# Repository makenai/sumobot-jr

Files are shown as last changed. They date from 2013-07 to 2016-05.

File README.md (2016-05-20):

# Sumobot Jr.

Sumobot Jr. is an open source sumobot design made for [Nodebots Day](http://nodebotsday.com). Most existing sumo kits cost between $99 and $160. Since we're trying to keep our event costs down, I decided to try to design a bot that could be put together for around $50 including the cost of the Arduino. The name and design are inspired by the simplicity and zip-tied wooden beauty of the [Printrbot Jr](http://printrbot.com/).

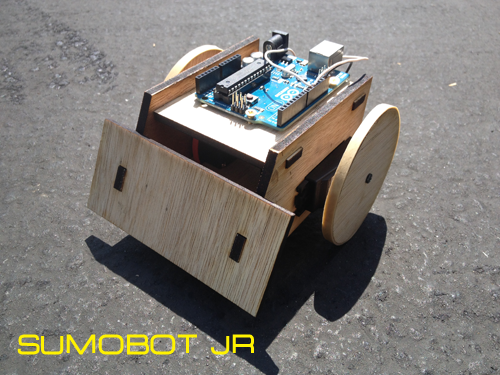
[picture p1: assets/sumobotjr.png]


## How ?

If you're planning on laser cutting the bots, you should use the OpenSCAD source file to generate a cutting plan for your specific type of laser cutter and material thickness. There's a wiki article for that!

[Laser Cutting with the OpenSCAD file](https://github.com/makenai/sumobot-jr/wiki/Working-with-the-OpenSCAD-file)

If you want to jump right into it, you can watch this instructional video, but note that you may not want to clip the wires if you plan to reuse the servos for something else:

[Sumobot Jr Assembly video for Nodebots Day 7/27](http://www.youtube.com/watch?v=0Q3hrKUwxDM)

[Customizing Sumobot Jr with Suziam and cats](http://www.youtube.com/watch?v=BB0vihv9ylM)

[IKEA-style Assembly Instruction Card](http://makenai.github.io/sumobot-jr/sumobot-instructions.pdf)

[Microsoft's version for Build 2015 on Raspberry Pi + Windows 10](https://www.youtube.com/watch?v=aKCieb-Gf2g)

[Katie K's No Solder Guide](http://katiek2.github.io/sumobot-nosolder/)

[Frank Hunleth's Arduino Mini Shield](https://oshpark.com/shared_projects/TEsKZkdg)

[Norfolk.js's Shopping List](https://github.com/norfolkjs/general-info/wiki/Norfolk.js-SumoBot-Kits)

[Sidepart adaptors for MG-6-48 DC-Motors from ghtomcat](https://github.com/ghtomcat/sumobot)

The main part of the design is a cutting sheet in EPS file format that is designed to be used with a laser cutter. You can find it in the cutting_plans directory. If you don't have a laser cutter, you can use a CNC, tape your printout to balsa wood and go at it with an x-acto knife, or send it to a laser cutting service like [Ponoko](https://www.ponoko.com/) and get the sheet done for about $10.

There is also a directory called 3d_print that contains an STL file for a ball caster designed by [sliptonic](http://www.thingiverse.com/thing:13782) - the STL is set up for a 16mm ball bearing, but you can make one for other sizes with the included OpenSCAD file.

**NEW** Microsoft has created a tutorial and version of the bot kit for [Build 2015](http://www.buildwindows.com/). You can find their version of the cutting plan for Ponoko in this repository, and also check out their [tutorial using Raspberry Pi and Windows 10](http://microsoft.hackster.io/windowsiot/robot-kit).

There is a completely 3D printable version available at [Thingiverse](http://www.thingiverse.com/thing:357369) now.

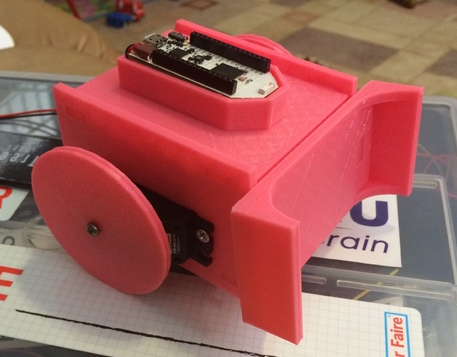
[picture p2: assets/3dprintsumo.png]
[](http://www.thingiverse.com/thing:357369)

## What if I don't have a Laser Cutter / 3D Printer?!

Neither do I! The best way to get some help creating the parts is to look up your local [Hackerspace or Makerspace ](http://hackerspaces.org) and connect with them. I belong to a fantastic hackerspace in Las Vegas called [SYN Shop](http://synshop.org)!

[](http://synshop.org)

If you don't have a hackerspace nearby, you can also use a mail order service like [Ponoko](http://ponoko.com) that does both 3D printing and laser cutting.

## Other Parts Needed

+ [Arduino](https://www.pololu.com/product/2191) - ~$25
+ [4xAA battery holder](http://www.amazon.com/gp/product/B007Q2NR1O/ref=oh_aui_search_detailpage?ie=UTF8&amp;psc=1) - $2
+ 2 Zip ties - ?
+ 5 \#4 3/8" wood screws - ?
+ Thick rubber bands - ?
+ 2 continuous servo motors like [Futaba S148](http://www.pololu.com/catalog/product/536) or the ones from [SpringRC](http://www.pololu.com/product/1248) - $24-$28
+ Some wire or leads
+ 16mm ball bearing - ?

## No-solder Wiring Diagram (thanks @katiek2)



That's about it! Connect the red and black leads on the servos together, then connect them to the + and - terminals on the battery holder respectively. Then connect the black leads and - terminal to the ground of the Arduino. Finally, the white leads of each motor go to pins 9 and 10 (or whatever you like) on the Arduino - you're done!

## Sample Code

To run the sample code for the Sumobot Jr., you will first need to install [Node.js](http://nodejs.org/) and [git](https://git-scm.com).

Open a terminal application and clone this repository:
```
git clone https://github.com/makenai/sumobot-jr
```

Navigate to the code folder:
```
cd code_example
```

Install code dependencies:

```
npm i
```

Run the code:

```
node sumobot.js
```

## License

[Creative Commons - Attribution - ShareAlike 3.0](http://creativecommons.org/licenses/by-sa/3.0/)

You are free to:

+ to Share — to copy, distribute and transmit the work, and
+ to Remix — to adapt the work
+ Under the following conditions:
    + Attribution — You must attribute the work in the manner specified by the author or licensor (but not in any way that suggests that they endorse you or your use of the work)
    + Share Alike — If you alter, transform, or build upon this work, you may distribute the resulting work only under the same, similar or a compatible license.

With the understanding that:

+ Waiver — Any of the above conditions can be waived if you get permission from the copyright holder.
+ Other Rights — In no way are any of the following rights affected by the license:
    + your fair dealing or fair use rights;
    + the author's moral rights; and
    + rights other persons may have either in the work itself or in how the work is used, such as publicity or privacy rights.

## Credits

Made by

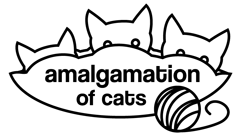
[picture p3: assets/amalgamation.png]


Design by [@makenai](http://twitter.com/makenai) with feedback and ideas from [@noopkat](http://twitter.com/noopkat) aka (by their powers combined) Amalgamation of Cats.

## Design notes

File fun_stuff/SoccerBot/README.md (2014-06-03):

##SoccerBot Mod

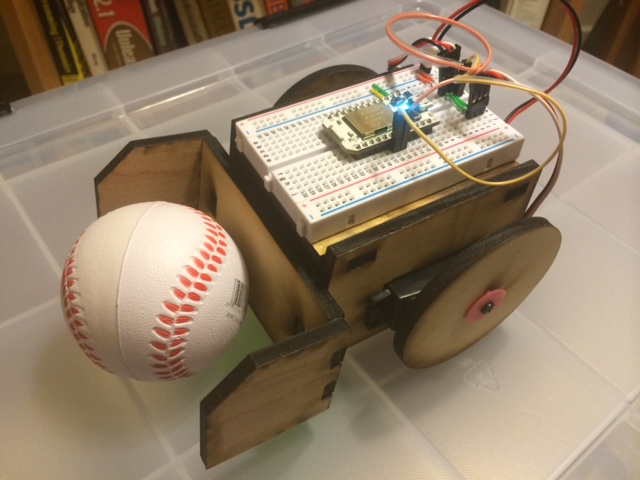
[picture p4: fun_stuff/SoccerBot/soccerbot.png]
SoccerBot


These modifications were created quickly and dirtily for the [JSConf 2014](http://2014.jsconf.us/) SoccerBot tournament. Just replacement wheels, shovel and a 3D printable wheel hub that is an improvement over the old wooden method!

Video (https://www.youtube.com/watch?v=CcCwjnWBoJ8)

Want to see the matches?

Video (https://www.youtube.com/watch?v=kE-g8LFVeYw)

Video (https://www.youtube.com/watch?v=HgWbxDNJleQ)

Video (https://www.youtube.com/watch?v=ViGQqndk6Og)

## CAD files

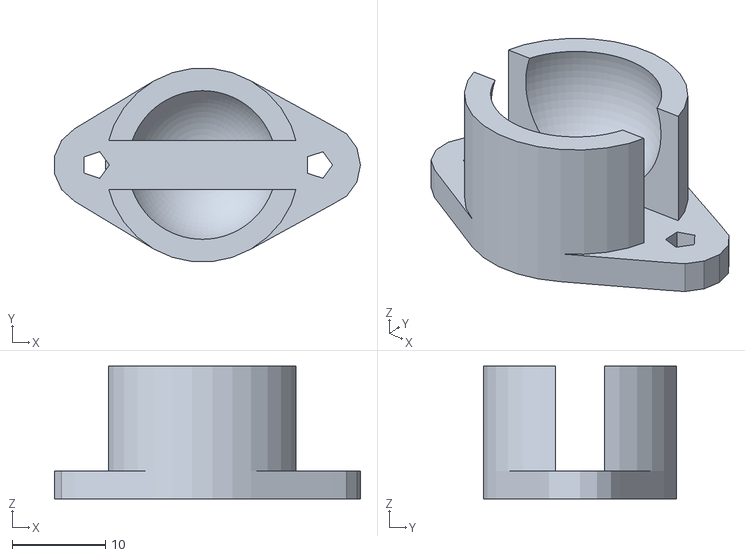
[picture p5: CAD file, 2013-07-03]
3d_print/BallCaster.stl
32.9 x 20.8 x 14.3

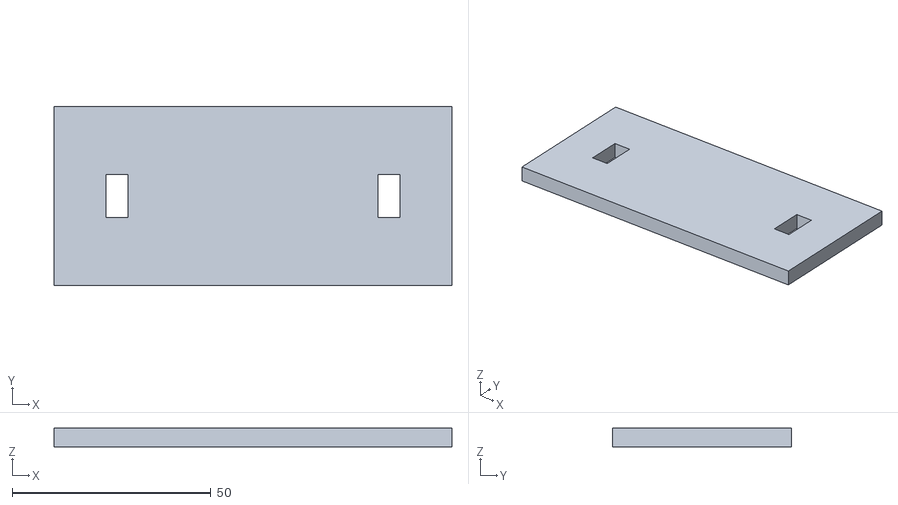
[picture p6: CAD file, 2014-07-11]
3d_print/sumobot/front-flat.stl
100.0 x 45.0 x 4.75

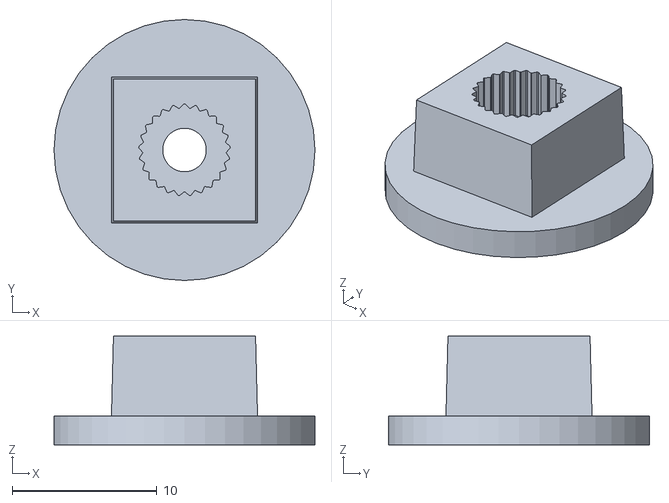
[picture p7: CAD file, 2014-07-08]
fun_stuff/SoccerBot/WheelHub.stl
18.0 x 18.0 x 7.50

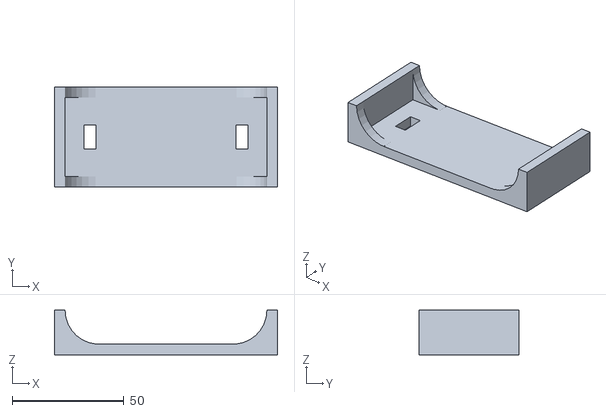
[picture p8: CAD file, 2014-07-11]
3d_print/sumobot/front-curved.stl
100.0 x 45.0 x 20.0

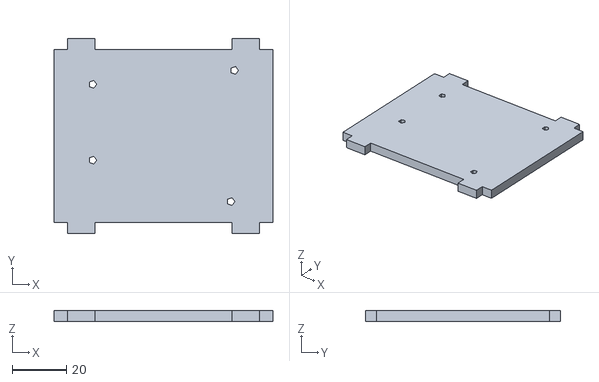
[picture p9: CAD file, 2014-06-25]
3d_print/sumobot/top-arduino.stl
80.5 x 71.5 x 4.00

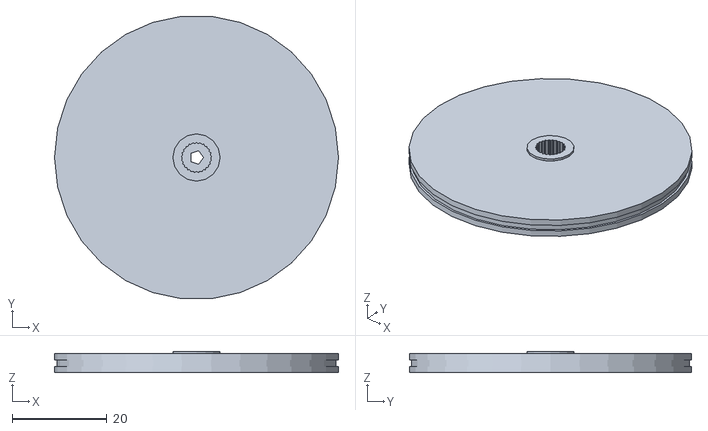
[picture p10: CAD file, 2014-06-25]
3d_print/sumobot/wheel.stl
60.0 x 59.7 x 4.50

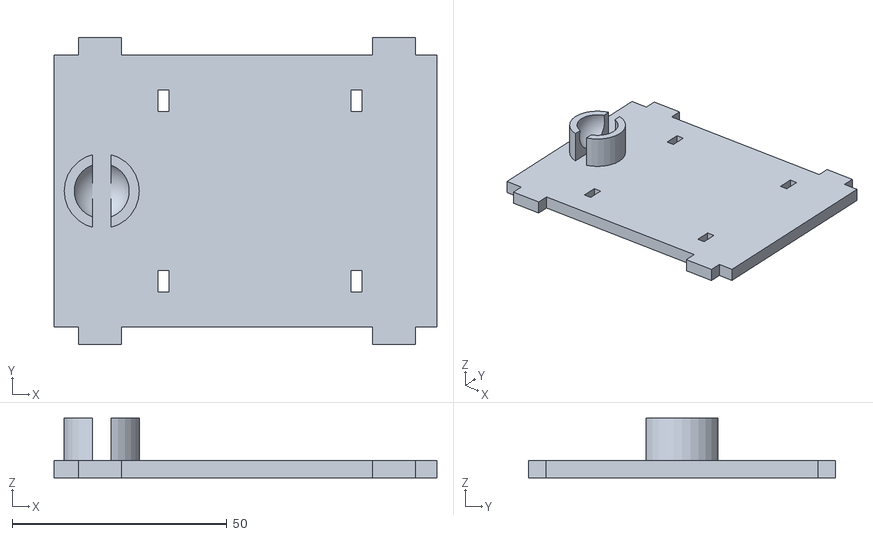
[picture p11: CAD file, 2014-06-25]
3d_print/sumobot/bottom.stl
89.3 x 71.5 x 13.9

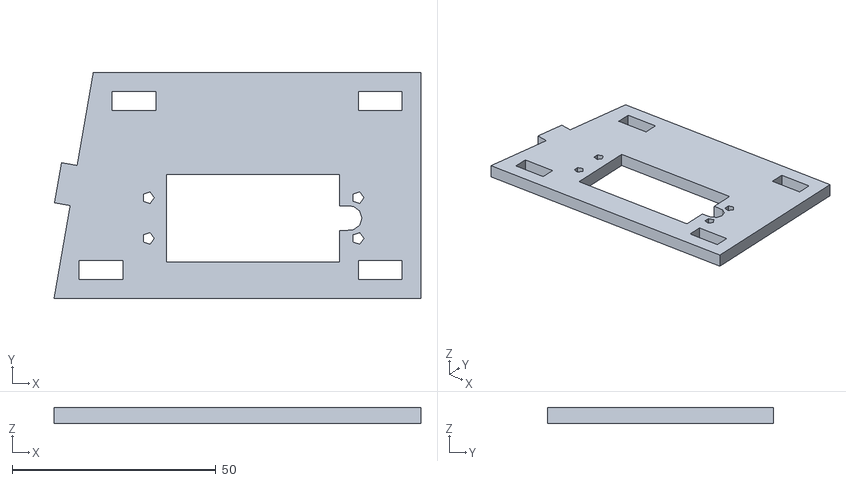
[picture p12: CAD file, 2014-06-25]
3d_print/sumobot/side.stl
90.1 x 55.5 x 4.00

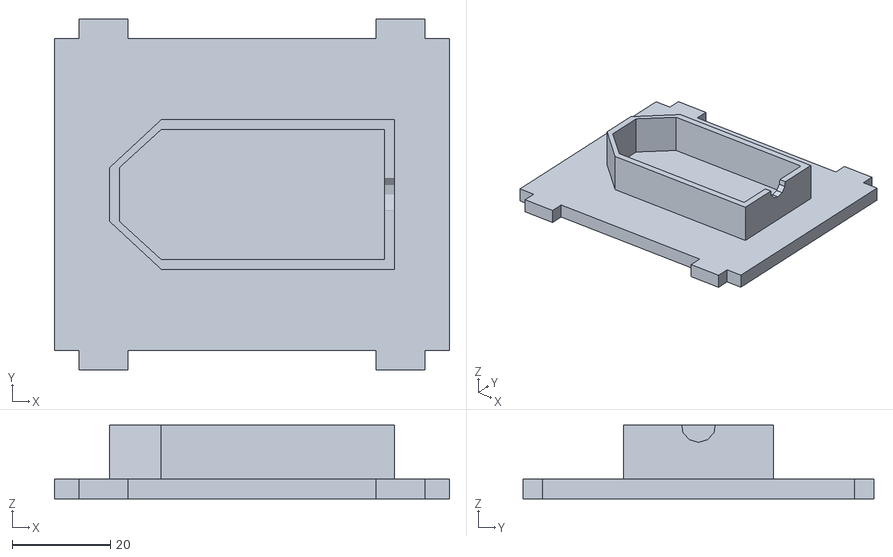
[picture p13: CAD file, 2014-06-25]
3d_print/sumobot/top-pinoccio.stl
80.5 x 71.5 x 15.0

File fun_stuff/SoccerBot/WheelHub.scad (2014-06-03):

/**
 *  Parametric servo arm generator for OpenScad
 *  Générateur de palonnier de servo pour OpenScad
 *
 *  Copyright (c) 2012 Charles Rincheval.  All rights reserved.
 *
 *  This library is free software; you can redistribute it and/or
 *  modify it under the terms of the GNU Lesser General Public
 *  License as published by the Free Software Foundation; either
 *  version 2.1 of the License, or (at your option) any later version.
 *
 *  This library is distributed in the hope that it will be useful,
 *  but WITHOUT ANY WARRANTY; without even the implied warranty of
 *  MERCHANTABILITY or FITNESS FOR A PARTICULAR PURPOSE.  See the GNU
 *  Lesser General Public License for more details.
 *
 *  You should have received a copy of the GNU Lesser General Public
 *  License along with this library; if not, write to the Free Software
 *  Foundation, Inc., 51 Franklin St, Fifth Floor, Boston, MA  02110-1301  USA
 *
 *  Last update :
 *  https://github.com/hugokernel/OpenSCAD_ServoArms
 *
 *  http://www.digitalspirit.org/
 */

$fn = 40;

/**
 *  Clear between arm head and servo head
 *  With PLA material, use clear : 0.3, for ABS, use 0.2
 */
SERVO_HEAD_CLEAR = 0.2;

/**
 *  Head / Tooth parameters
 *  Futaba 3F Standard Spline
 *  http://www.servocity.com/html/futaba_servo_splines.html
 *
 *  First array (head related) :
 *  0. Head external diameter
 *  1. Head heigth
 *  2. Head thickness
 *  3. Head screw diameter
 *
 *  Second array (tooth related) :
 *  0. Tooth count
 *  1. Tooth height
 *  2. Tooth length
 *  3. Tooth width
 */
FUTABA_3F_SPLINE = [
    [6, 4, 1.1, 2.5],
    [25, 0.3, 0.7, 0.1]
];

module servo_futaba_3f(length, count) {
    servo_arm(FUTABA_3F_SPLINE, [length, count]);
}

/**
 *  If you want to support a new servo, juste add a new spline definition array
 *  and a module named like servo_XXX_YYY where XXX is servo brand and YYY is the
 *  connection type (3f) or the servo type (s3003)
 */

module servo_standard(length, count) {
    servo_futaba_3f(length, count);
}

/**
 *  Tooth
 *
 *    |<-w->|
 *    |_____|___
 *    /     \  ^h
 *  _/       \_v
 *   |<--l-->|
 *
 *  - tooth length (l)
 *  - tooth width (w)
 *  - tooth height (h)
 *  - height
 *
 */
module servo_head_tooth(length, width, height, head_height) {
    linear_extrude(height = head_height) {
        polygon([[-length / 2, 0], [-width / 2, height], [width / 2, height], [length / 2,0]]);
    }
}

/**
 *  Servo head
 */
module servo_head(params, clear = SERVO_HEAD_CLEAR) {

    head = params[0];
    tooth = params[1];

    head_diameter = head[0];
    head_heigth = head[1];

    tooth_count = tooth[0];
    tooth_height = tooth[1];
    tooth_length = tooth[2];
    tooth_width = tooth[3];

    % cylinder(r = head_diameter / 2, h = head_heigth + 1);

    cylinder(r = head_diameter / 2 - tooth_height + 0.03 + clear, h = head_heigth);

    for (i = [0 : tooth_count]) {
        rotate([0, 0, i * (360 / tooth_count)]) {
            translate([0, head_diameter / 2 - tooth_height + clear, 0]) {
                servo_head_tooth(tooth_length, tooth_width, tooth_height, head_heigth);
            }
        }
    }
}

/**
 *  Servo hold
 *  - Head / Tooth parameters
 *  - Arms params (length and count)
 */
module servo_arm(params, arms) {

    head = params[0];
    tooth = params[1];

    head_diameter = head[0];
    head_heigth = head[1];
    head_thickness = head[2];
    head_screw_diameter = head[3];

    tooth_length = tooth[2];
    tooth_width = tooth[3];

    arm_length = arms[0];
    arm_count = arms[1];

    /**
     *  Servo arm
     *  - length is from center to last hole
     */
    module arm(tooth_length, tooth_width, head_height, head_heigth, hole_count = 1) {

        arm_screw_diameter = 2;

        difference() {
            union() {
                cylinder(r = tooth_width / 2, h = head_heigth);

                linear_extrude(height = head_heigth) {
                    polygon([
                        [-tooth_width / 2, 0], [-tooth_width / 3, tooth_length],
                        [tooth_width / 3, tooth_length], [tooth_width / 2, 0]
                    ]);
                }

                translate([0, tooth_length, 0]) {
                    cylinder(r = tooth_width / 3, h = head_heigth);
                }

                if (tooth_length >= 12) {
                    translate([-head_heigth / 2 + 2, 3.8, -4]) {
                        rotate([90, 0, 0]) {
                            rotate([0, -90, 0]) {
                                linear_extrude(height = head_heigth) {
                                    polygon([
                                        [-tooth_length / 1.7, 4], [0, 4], [0, - head_height + 5],
                                        [-2, - head_height + 5]
                                    ]);
                                }
                            }
                        }
                    }
                }
            }

            // Hole
            for (i = [0 : hole_count - 1]) {
                //translate([0, length - (length / hole_count * i), -1]) {
                translate([0, tooth_length - (4 * i), -1]) {
                    cylinder(r = arm_screw_diameter / 2, h = 10);
                }
            }

            cylinder(r = head_screw_diameter / 2, h = 10);
        }
    }

    difference() {
        translate([0, 0, 0.1]) {
            cylinder(r = head_diameter / 2 + head_thickness, h = head_heigth + 1);
        }

        cylinder(r = head_screw_diameter / 2, h = 10);

        servo_head(params);
    }

    arm_thickness = head_thickness;

    // Arm
    translate([0, 0, head_heigth]) {
        for (i = [0 : arm_count - 1]) {
            rotate([0, 0, i * (360 / arm_count)]) {
                arm(arm_length, head_diameter + arm_thickness * 2, head_heigth, 2);
            }
        }
    }
}

module wheelhub() {
	translate([0,0,1])	
	difference() {
		union() {
			hull() {
				cube([10.1,10.1,1],center=true);
				translate([0,0,6]) {
					cube([9.8,9.8,1],center=true);
				}
			}
			cylinder(d=18,h=2,center=true);
		}
		translate([0,0,-10]) cylinder(d=3,h=20);
		translate([0,0,-1.1]) cylinder(d=4,h=1);
		translate([0,0,3]) servo_head(FUTABA_3F_SPLINE);
	}
}

wheelhub();

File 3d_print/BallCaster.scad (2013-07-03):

WallThickness = 2;
BallSize = 15.88;
Airgap = .5;
Mount = 3;
TotalHeight = 19.5;
MountScrewRad = 1.5;  //3mm screw
BallProtrude = .33; //percentage of ball radius sticking out 

MountType = 1;  //1=ears  2=center screw
ScrewSpacing = 25;


cylheight = TotalHeight;
cylrad = (BallSize/2) + WallThickness + Airgap;
echo (cylheight);
difference () {
	cylinder(r1 = cylrad , r2 = cylrad,  cylheight - (BallSize*BallProtrude));

	translate([0,0,TotalHeight - BallSize/2]) {
		cube(size = [cylrad*2+5, cylrad/2, BallSize*1.25], center = true );
		}

	translate([0,0,TotalHeight - (BallSize/2)]) {
		sphere (BallSize/2+Airgap, $fa=5, $fs=0.1);
		}
	}

difference (){
	linear_extrude(height=Mount)
	hull() {
		translate([ScrewSpacing/2,0,0]) {
			circle(  MountScrewRad*3);
			}
  		translate([1-ScrewSpacing/2,0,0]) {
			circle( MountScrewRad*3);
   			}
		circle( cylrad);
		}

	translate([ScrewSpacing/2,0,0]) {
		cylinder(r1 = MountScrewRad, r2 = MountScrewRad, h= Mount+2);
		}
  	translate([1-ScrewSpacing/2,0,0]) {
		cylinder(r1 = MountScrewRad, r2 = MountScrewRad, h= Mount+2);
   		}
}

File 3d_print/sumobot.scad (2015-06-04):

/*
 * =============================================================================
 * SumoBot Kit Master OpenSCAD File
 * =============================================================================
 * All measurements are in mm, because go metric or go home.
 */

 /* Build Flags - Variables to programatically select which part to output */

  build_laser_sheet = 1;
  build_wheel = 0;
  build_top = 0;
  build_shovel = 0;
  build_bottom = 0;
  build_side = 0;

/* Features Flags */

  // For 3D printing, we can have a curved or flat shovel
  curved_shovel = 0;

  // For 3D printing, we can include a ball caster on the bottom
  built_in_caster = 0;

  // For 3D printing, we can have a built in wheel hub
  built_in_hub = 1;

  // For 3D printing, we can select a pinoccio mount for the top
  pinoccio_top = 0;

/* Parameters */

  // Kerf is the amount of space removed by a cutting tool. I use it
  // here to describe how much space to leave between tabs and space.
  // For laser cutters, I use 0.05, for 3D printers I use 0.375
  kerf = 0.05;

  // How thick is the material? This also is the tab height.
  material_thickness = 4.75;

  // How high is the battery case?
  battery_case_height = 16;

  // How large is our servo hole?
  servo_height = 21.5;
  servo_length = 42.5;

  // How long is the sumo bot?
  sled_length = 80.5;

  // How wide is the sumo bot?
  sled_width = 63.5;

  // How close to the edge of the material do we place a tab?
  tab_edge_distance = 5;

  // How long are our tabs?
  tab_length = 10;

  // What is the angle that the sumobot shovel?
  ramp_angle = 80;

  // How wide is the shovel?
  shovel_width = 100;

  // How high is the shovel?
  shovel_height = 45;

  // Only for a 3D printed, curved shovel, how tall is the side?
  shovel_side_height = 20;

  // How big are our ziptie holes?
  ziptie_height = 5;
  ziptie_width = 2.5;

  // How big are the screw holes? 2.25mm is good for #4 wood screws
  screw_diameter = 2.25;

  // How far apart are our ball caster holes?
  caster_screw_spacing = 25;

  // How far back from the front do we place the caster?
  caster_position = 12;

  // How big are our wheels?
  wheel_radius = 30;

  // Caster Settings
  Caster_WallThickness = 2;
  Caster_BallSize = 12.5;
  Caster_Airgap = .5;
  Caster_TotalHeight = 14;
  Caster_BallProtrude = .33;

  // Servo Wheel
  SERVO_HEAD_CLEAR = 0.2;
  FUTABA_3F_SPLINE = [
      [6, 4, 1.1, 2.5],
      [25, 0.3, 0.7, 0.1]
  ];
  FUTABA_3F_SPLINE_KERF = [
      [6-(kerf/2), 4, 1.1, 2.5],
      [25, 0.3, 0.7, 0.1]
  ];

/* Calculated Values */

  // Tab spacing account for kerf
  tab_spacing = kerf * 2;

  // We figure out the side based on a snug fit for the battery case
  sled_height = ((material_thickness + tab_edge_distance) * 2 ) +
  	servo_height + battery_case_height;

  // Length of the ramp (bottom of the right triangle) depends on the angle
  ramp_length = cos( ramp_angle ) * sled_height;

  // We want to place the tab the correct tab distance on the bottom, so we need
  // to cut into the distance taken up by the ramp.
  ramp_tab_distance = cos(ramp_angle)*( tab_edge_distance + material_thickness);

  // The length of the sled plus the length of the ramp
  side_length = sled_length + ( cos( ramp_angle ) * (sled_height - tab_edge_distance) );

/* Utility Modules */

// A hole for a screw.
module screw_hole() {
	circle(d=screw_diameter);
}

// Male side of the tab
module tab() {
	square([tab_length, material_thickness]);
}

// Female side of the tab
module tab_hole() {
	translate([tab_spacing/-2,tab_spacing/-2])
		square([tab_length + tab_spacing, material_thickness +tab_spacing]);
}

// A ziptie hole
module ziptie_hole() {
	square([ziptie_width,ziptie_height]);
}

// Built-in ball caster
module caster() {
	cylheight = Caster_TotalHeight;
	cylrad = (Caster_BallSize/2) + Caster_WallThickness + Caster_Airgap;
	difference () {
		cylinder(r1 = cylrad , r2 = cylrad,  cylheight - (Caster_BallSize*Caster_BallProtrude));
		translate([0,0,Caster_TotalHeight - Caster_BallSize/2]) {
			cube(size = [cylrad*2+5, cylrad/2, Caster_BallSize*1.25], center = true );
		}
		translate([0,0,Caster_TotalHeight - (Caster_BallSize/2)]) {
			sphere (Caster_BallSize/2+Caster_Airgap, $fa=5, $fs=0.1);
		}
	}
}

// Servo mounting hole including a circular cutout for the wires
module servo_hole() {
	square([servo_length, servo_height]);
	// screw holes
	translate([-4.5,(servo_height/2)+5])
		screw_hole();
	translate([-4.5,(servo_height/2)-5])
		screw_hole();
	translate([servo_length+4.5,(servo_height/2)+5])
		screw_hole();
	translate([servo_length+4.5,(servo_height/2)-5])
		screw_hole();
	// wire hole
	hull() {
		translate([servo_length-1,servo_height/2])
			square(6,center=true);
		translate([servo_length+2.5,servo_height/2])
			circle(3,center=true);
	}

}

// Mounting holes for an arduino
module arduino_holes() {
	translate([-26.05,-24.1]) {
		translate([0, 15.2]) screw_hole();
		translate([0, 43.1]) screw_hole();
		translate([50.8, 0]) screw_hole();
		translate([52.1, 48.2]) screw_hole();
	}
}

// A special pinoccio shaped mount for the top of the bot
module pinoccio_mount() {
	height = 11;
	base_width = 26.5;
	base_length = 45.5;
	bevel_width = 11;
	bevel_length =8.5;
	wall_thickness = 2;
	plug_hole_size = 3.5;

	translate([base_length/-2-bevel_length/-2,-base_width/2])
	difference() {
		linear_extrude(height)
		hull() {
			translate([0,-wall_thickness])
				square([base_length + wall_thickness,base_width + wall_thickness*2]);
 			translate([-bevel_length - wall_thickness,base_width/2-bevel_width/2])
				square(bevel_width);
		}
		translate([0,0,-1])
		linear_extrude(height+2)
		hull() {
			square([base_length,base_width]);
			translate([-bevel_length,base_width/2-bevel_width/2])
				square(bevel_width);
		}
		translate([base_length-1, base_width/2,height])
			rotate([0,90])
			cylinder(r=plug_hole_size,h=wall_thickness+2);
	}
}

// The little curved part on the side of the curved shovel
module sloped_support(size) {
	difference() {
		cube([size,material_thickness,size]);
		translate([size,material_thickness+1,size])
			rotate([90])
			cylinder(r=size-material_thickness,h=material_thickness+2);
	}
}

// Side for a curved shovel (___)
module shovel_side() {
	cube([material_thickness,shovel_height,shovel_side_height]);
	sloped_support(shovel_side_height);
	translate([0,shovel_height-material_thickness])
		sloped_support(shovel_side_height);
}

module servo_head_tooth(length, width, height, head_height) {
    linear_extrude(height = head_height) {
        polygon([[-length / 2, 0], [-width / 2, height], [width / 2, height], [length / 2,0]]);
    }
}

// The little part that you can attach servo hubs to on a servo, used for the
// built in hub option of the wheel.
module servo_head(params, clear = SERVO_HEAD_CLEAR) {

    head = params[0];
    tooth = params[1];

    head_diameter = head[0];
    head_heigth = head[1];

    tooth_count = tooth[0];
    tooth_height = tooth[1];
    tooth_length = tooth[2];
    tooth_width = tooth[3];

	union() {
    cylinder(r = head_diameter / 2 + 0.1, h = head_heigth + 1);

    cylinder(r = head_diameter / 2 - tooth_height + 0.03 + clear, h = head_heigth);

    for (i = [0 : tooth_count]) {
        rotate([0, 0, i * (360 / tooth_count)]) {
            translate([0, head_diameter / 2 - tooth_height + clear, 0]) {
                servo_head_tooth(tooth_length, tooth_width, tooth_height, head_heigth);
            }
        }
    }
	}
}

// The little screw slot in the side of the sumo bot -
module wheel_screw_slot() {
	hull() {
		translate([0,0,-1])
			cylinder(d=screw_diameter,h=material_thickness+2);
		translate([0,8,-1])
			cylinder(d=screw_diameter,h=material_thickness+2);
	}
}

/* Parts */

// The side of the sumobot /___|
module side() {
	linear_extrude(height=material_thickness)
	difference() {

		union() {
			square([sled_length, sled_height]);
			polygon([[0,0], [0,sled_height], [-ramp_length,0]] );
			translate([-ramp_length/2,sled_height/2])
				rotate(ramp_angle)
				translate([-tab_length/2,-0.1])
				tab();
		}

		// Servo hole
		translate([sled_length - servo_length - tab_length - tab_edge_distance - tab_edge_distance,
				material_thickness + tab_edge_distance])
			servo_hole();

		// Bottom right
		translate([sled_length - tab_length - tab_edge_distance, tab_edge_distance])
			tab_hole();

		// Bottom Left
		translate([-ramp_length + ramp_tab_distance + tab_edge_distance,
				tab_edge_distance])
			tab_hole();

		// Top left
		translate([tab_edge_distance, sled_height - material_thickness - tab_edge_distance])
			tab_hole();

		// Top right
		translate([sled_length - tab_length - tab_edge_distance,
				sled_height - material_thickness - tab_edge_distance])
			tab_hole();
	}
}
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

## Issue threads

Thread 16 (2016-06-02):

Mounting hole options

dtex, 2016-06-02:
I'd like to add a parameter to the SCAD file for choosing different hole patterns for the top plate (Tessel 2 is my use case). Does that sound like a worthwhile PR?

makenai, 2016-06-02:
Yup - most certainly. Thanks for looking at the SCAD files instead of the vectors. :)

I think you should be able to add an parameter / method to it similar to the arduino and pinoccio ones here: https://github.com/makenai/sumobot-jr/blob/master/3d_print/sumobot.scad#L186

dtex, 2016-06-02:
Cool. I was thinking of adding a parameter like this:
````
// Mounting hole pattern
// valid values are "Arduino Uno", "Tessel 2"
hole_pattern = "Arduino Uno";
````
And then just add a conditional in ```top``` to call the right module.

dtex, 2016-06-05:
Hmmm, like most things it's never as easy as it seems. I had to make the sled wider to fit the mounting holes, but the GPIO ports are still kind of exposed (anything plugged in could be easily ripped out by another sumo).

Sigh...

I'll keep playing with it.

dtex, 2016-06-26:
I'm thinking it makes the most sense to have an option for Tessel mounting holes like we discussed, but then just have a note somewhere (the readme?) that gives the minimum sled width and a suggested sled length.

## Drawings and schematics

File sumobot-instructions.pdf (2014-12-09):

# SumoBot Kit

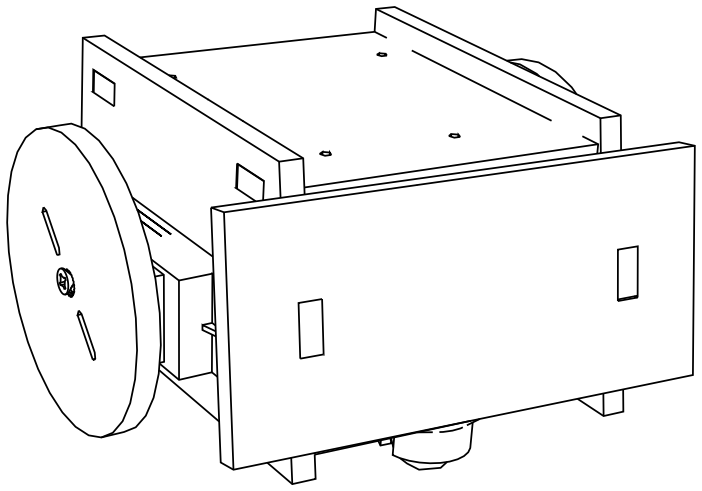
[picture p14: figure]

# http://sumobotkit.com

### (you can call it a PawelBot if you want to)

This simple yet versatile robot kit is ready to become your loyal companion! Unlike many robots you’ll see, this one is made of wood. That makes it very easy to glue, paint, drill, and customize to your heart’s content. There is a great personality in this wooden frame just waiting for you to release it!

See the assembly instructions on the flip side of this card. When it’s time to hook up a “brain” of your choosing, just remember:

- red (+) wires all go together
- black (-) wires go together and to a ground pin on your microcontroller
- white or yellow wires go to PWM capable pins on your microcontroller

If you find your motors move when you don’t want them to, you can center them with a screwdriver by turning the potentiometer on the back of each servo. Enjoy your new robot friend!

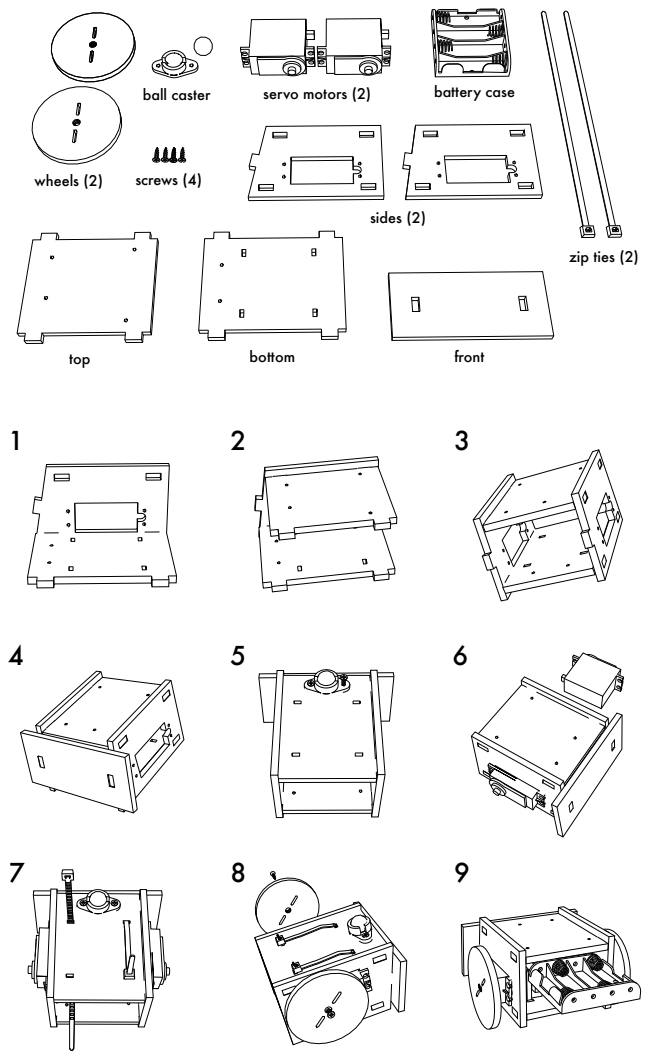
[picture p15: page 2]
wheels (2); screws (4); ball caster; servo motors (2); battery case; top; bottom; front; sides (2); zip ties (2)

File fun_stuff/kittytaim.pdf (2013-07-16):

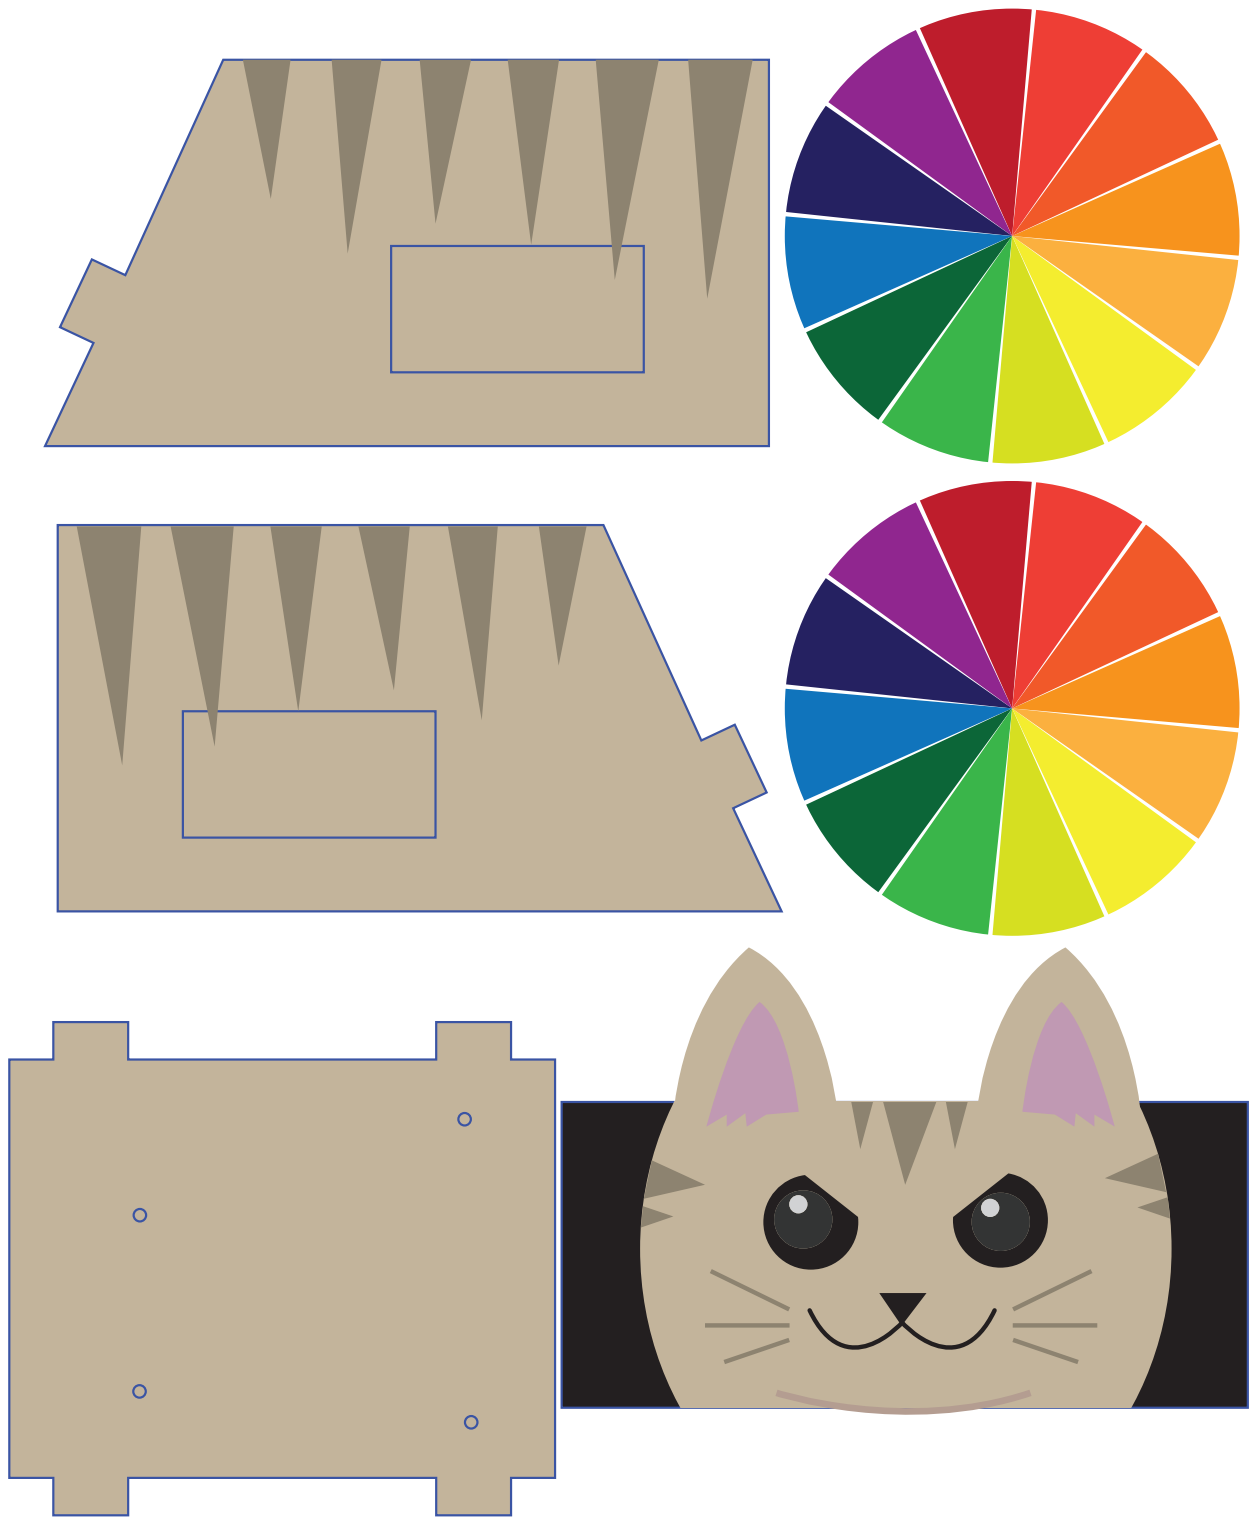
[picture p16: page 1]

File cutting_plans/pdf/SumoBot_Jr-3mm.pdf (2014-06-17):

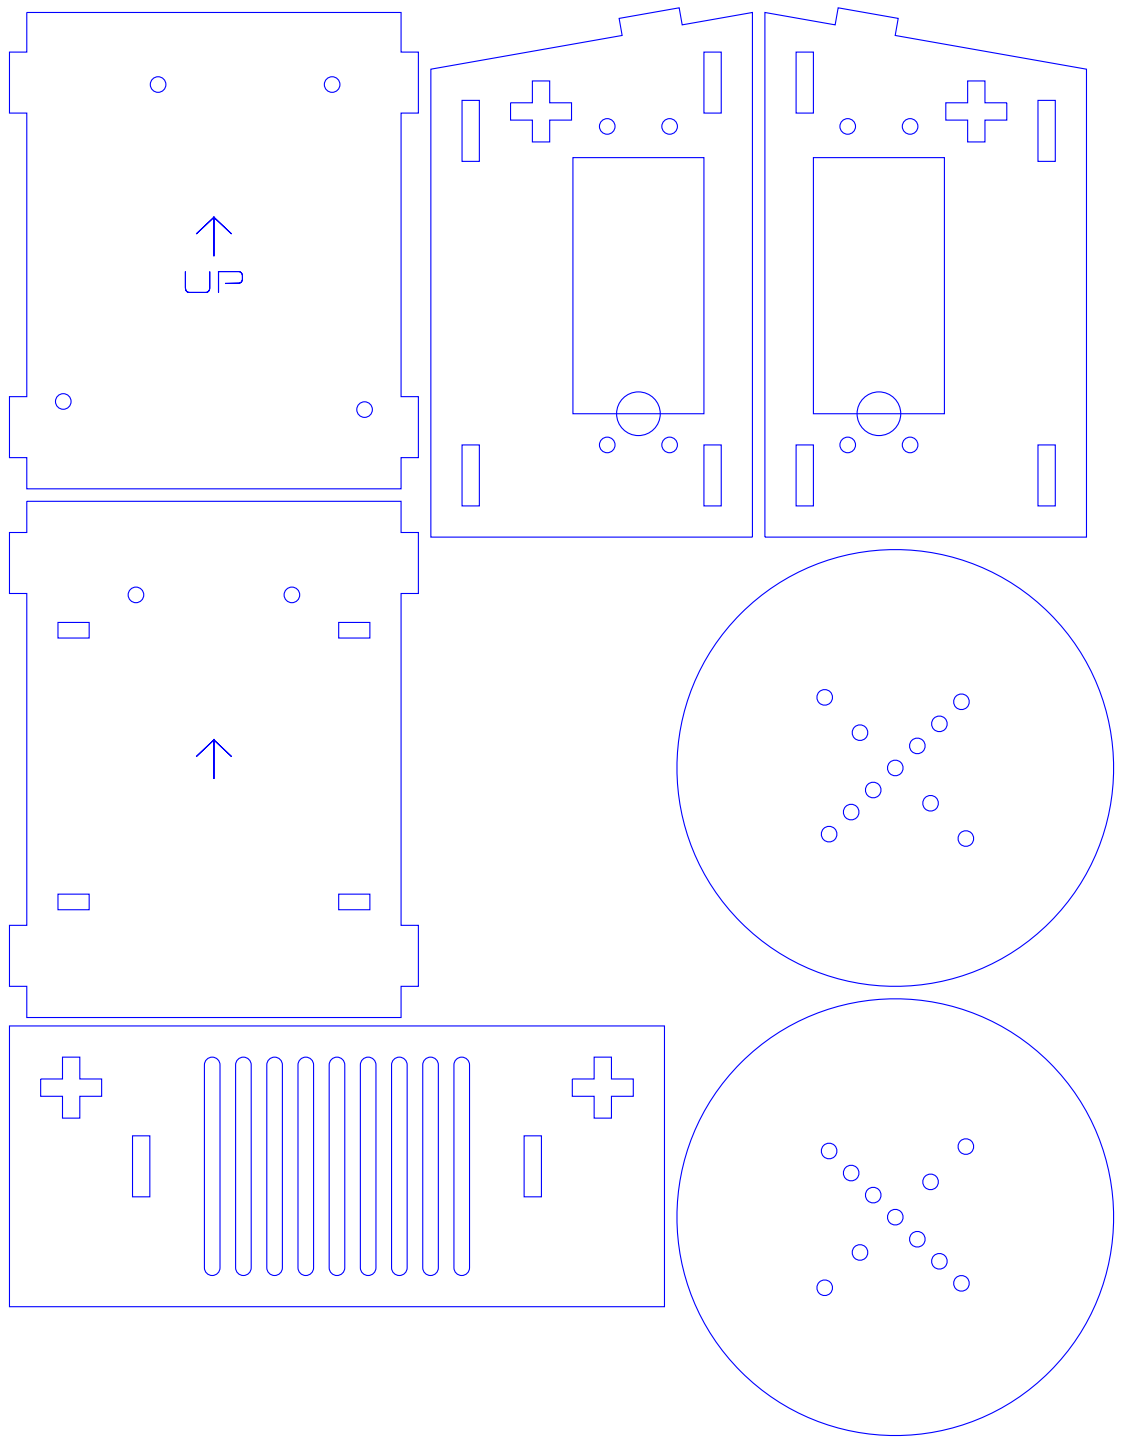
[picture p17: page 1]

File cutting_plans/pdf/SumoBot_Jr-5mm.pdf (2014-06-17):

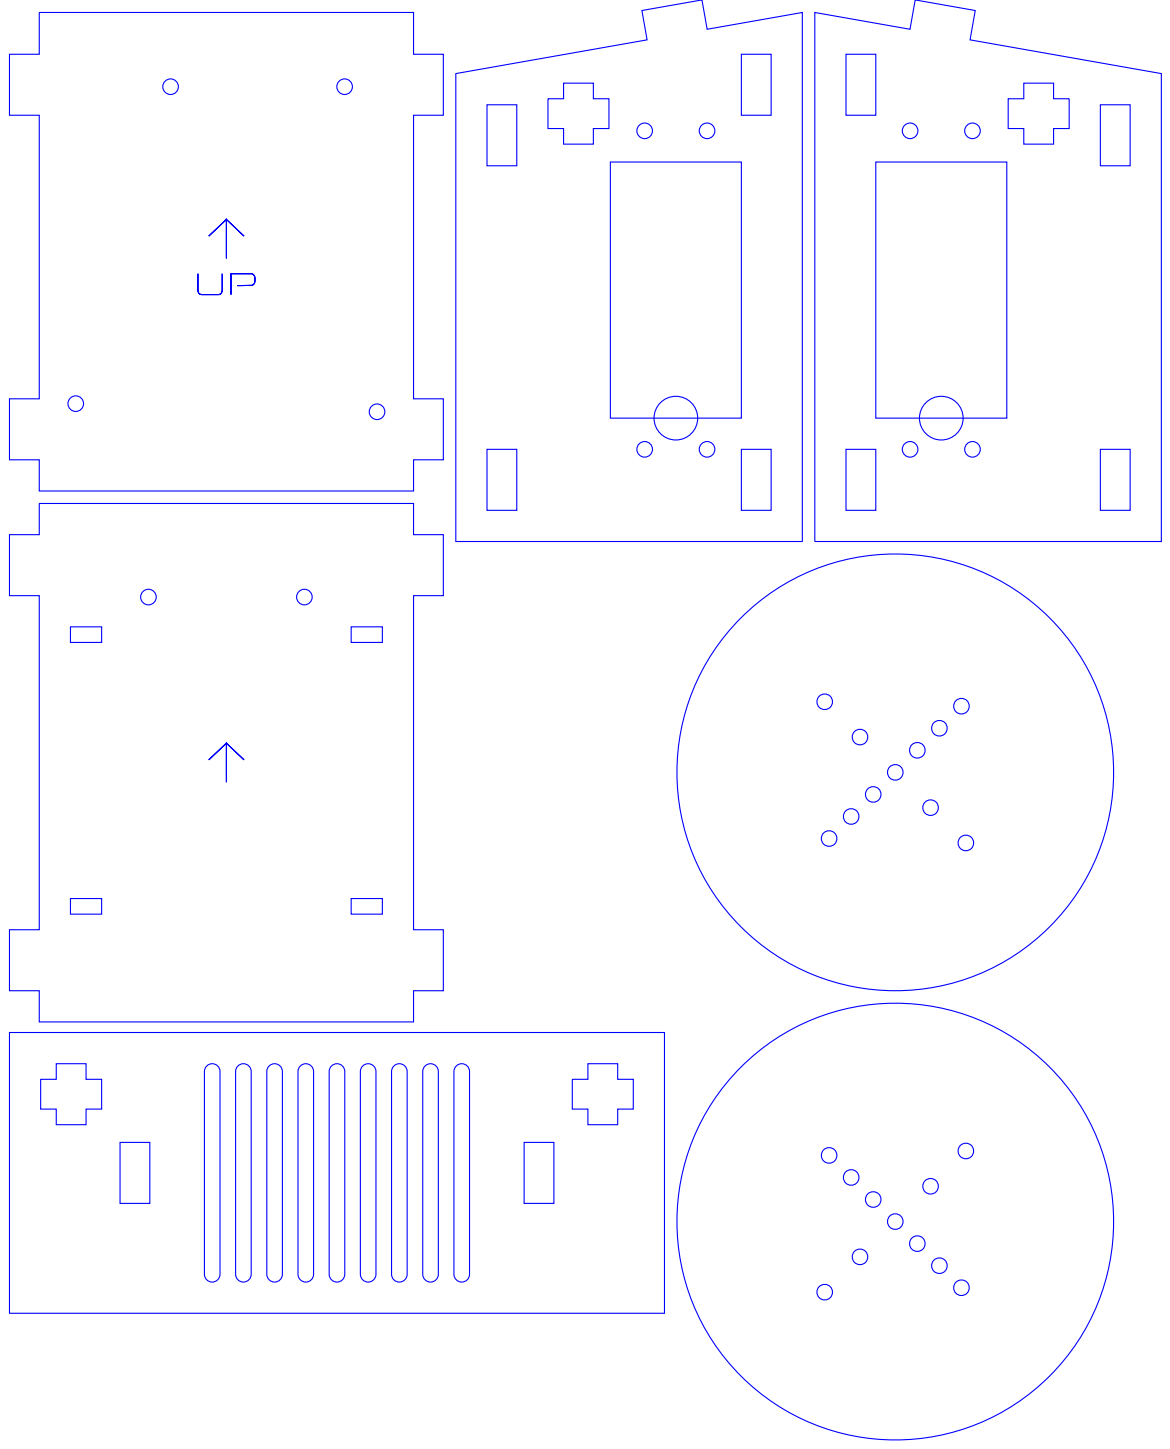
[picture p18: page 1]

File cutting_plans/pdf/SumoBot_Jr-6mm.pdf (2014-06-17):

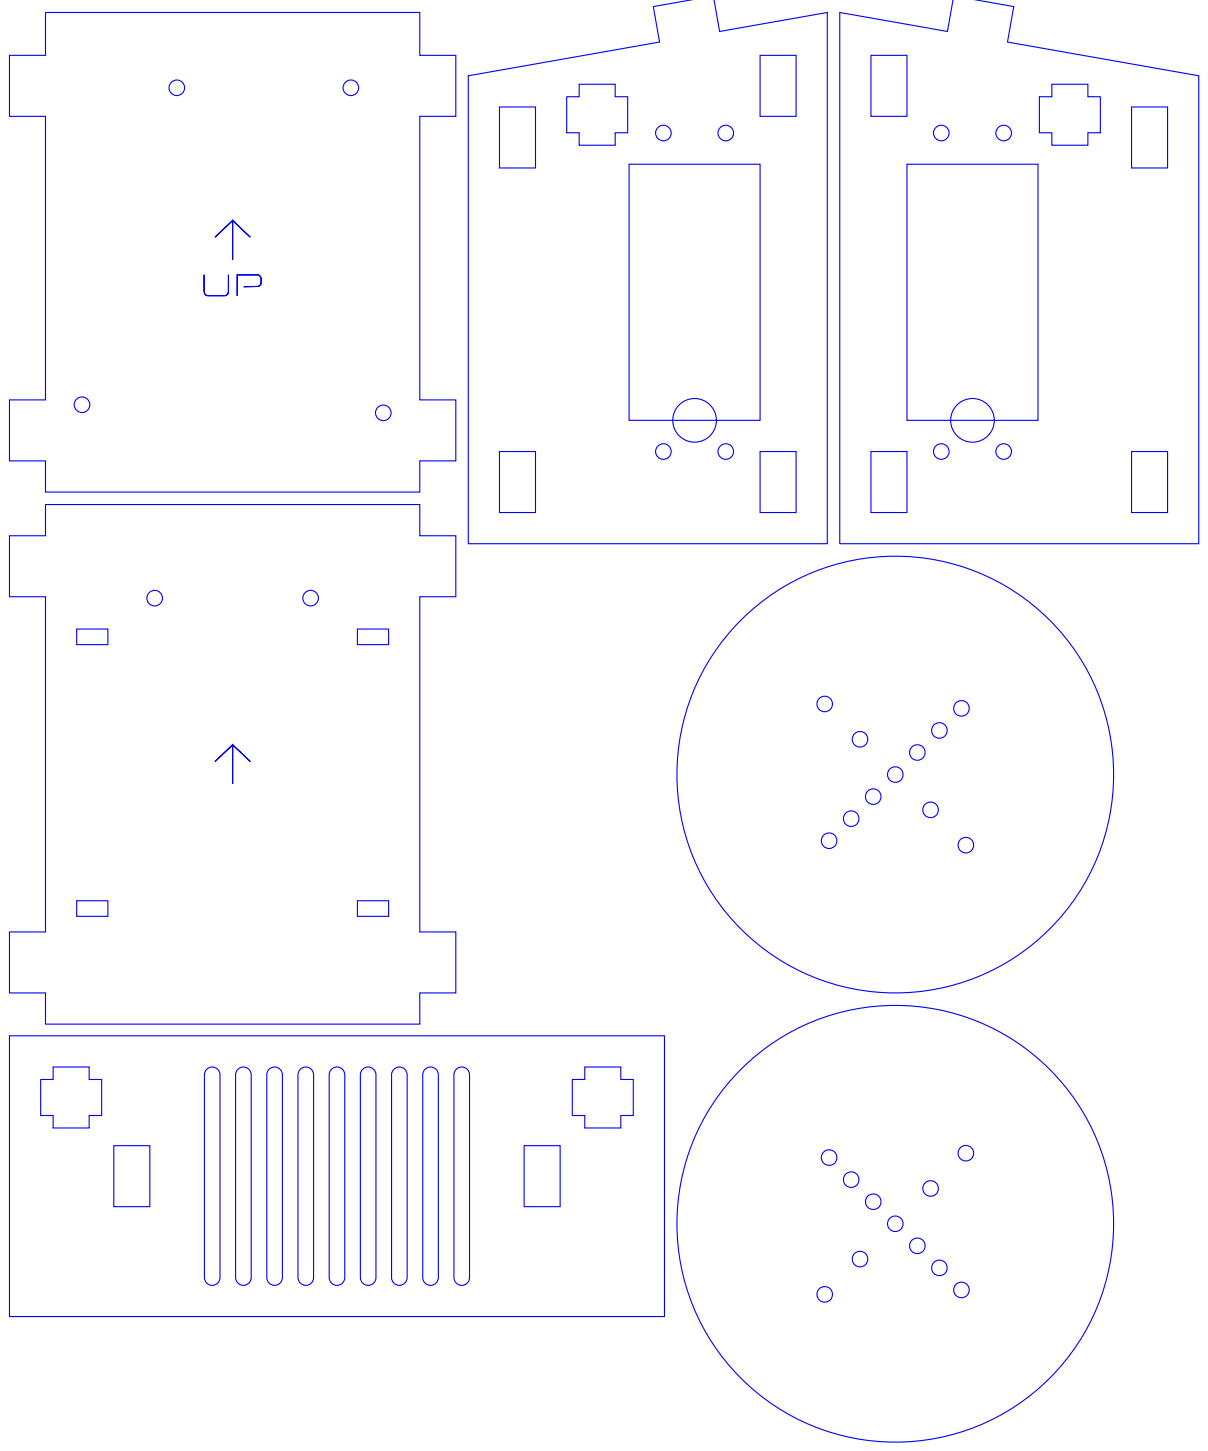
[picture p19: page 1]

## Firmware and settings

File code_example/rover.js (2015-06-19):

'use strict';

var five = require('johnny-five');
var board = new five.Board();
var keypress = require('keypress');

board.on('ready', function() {
  // Use your shield configuration from the list
  // http://johnny-five.io/api/motor/#pre-packaged-shield-configs
  var configs = five.Motor.SHIELD_CONFIGS.ADAFRUIT_V1;
  var motors = new five.Motors([
    configs.M1,
    configs.M2
  ]);

  this.repl.inject({
    motors: motors
  });

  console.log('Welcome to the Pee Wee Runt Rover!');
  console.log('Control the bot with the arrow keys, and SPACE to stop.');

  function forward() {
    console.log('Going forward');
    motors.fwd(255);
  }

  function backward() {
    console.log('Going backward');
    motors.rev(255);
  }

  function left() {
    console.log('Going left');
    motors[0].rev(200);
    motors[1].fwd(200);
  }

  function right() {
    console.log('Going right');
    motors[1].rev(200);
    motors[0].fwd(200);
  }

  function stop() {
    motors.stop();
  }

  keypress(process.stdin);
  process.stdin.resume();
  process.stdin.setEncoding('utf8');
  process.stdin.setRawMode(true);
  process.stdin.on('keypress', function (ch, key) {

    if ( !key ) { return; }

    if ( key.name === 'q' ) {

      console.log('Quitting');
      stop();
      process.exit();

    } else if ( key.name === 'up' ) {

      forward();

    } else if ( key.name === 'down' ) {

      backward();

    } else if ( key.name === 'left' ) {

      left();

    } else if ( key.name === 'right' ) {

      right();

    } else if ( key.name === 'space' ) {

      stop();

    }
  });
});

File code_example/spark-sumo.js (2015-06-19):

// ================================================
// Sumobot Jr demo program (wireless with Spark-IO)
// ================================================

'use strict';

var five = require('johnny-five');
var Spark = require('spark-io');
var keypress = require('keypress');

keypress(process.stdin);

var board = new five.Board({
  io: new Spark({
    token: process.env.SPARK_TOKEN,
    deviceId: process.env.SPARK_DEVICE_ID
  })
});

board.on('ready', function() {

  console.log('Welcome to Sumobot Jr, powered wirelessly with the Spark Core!')
  console.log('Control the bot with the arrow keys, and SPACE to stop.')

  var leftWheel = new five.Servo({ pin: 'D0', type: 'continuous' }).stop();
  var rightWheel = new five.Servo({ pin: 'D1', type: 'continuous' }).stop();

  process.stdin.resume();
  process.stdin.setEncoding('utf8');
  process.stdin.setRawMode(true);

  process.stdin.on('keypress', function (ch, key) {

    if ( !key ) { return; }

    if ( key.name === 'q' ) {

      console.log('Quitting');
      process.exit();

    } else if ( key.name === 'up' ) {

      console.log('Forward');
      leftWheel.ccw(0.9);
      rightWheel.cw(0.9);

    } else if ( key.name === 'down' ) {

      console.log('Backward');
      leftWheel.cw(0.9);
      rightWheel.ccw(0.9);

    } else if ( key.name === 'left' ) {

      console.log('Left');
      leftWheel.ccw(0.9);
      rightWheel.ccw(0.9);


    } else if ( key.name === 'right' ) {

      console.log('Right');
      leftWheel.cw(0.9);
      rightWheel.cw(0.9);

    } else if ( key.name === 'space' ) {

      console.log('Stopping');
      leftWheel.stop();
      rightWheel.stop();

    }

  });

});

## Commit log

2013-07-21 Adjusted distance of plow holes
2013-12-20 Added arduino mount holes
2013-12-26 Added more parameters. Using trig to figure out bottom plate height.
2013-12-26 Added ziptie holes
2013-12-27 Added screw holes for motor
2013-12-27 Various adjustments to wheels, ziptie holes, and motor holes
2013-12-28 Added accesory holes
2013-12-28 Moved accessory hole alignment
2013-12-28 Changed wheel orientation
2014-01-03 Removing pink box. Adding space to servo
2014-05-19 Example using Spark-IO for wireless SumoBot Jr
    Also added NPM package.json for dependencies
2014-05-20 avoid current bug with .ccw(1) on spark core
    [spark-sumo.js]
2014-06-01 Adding WIP OpenSCAD sumo
    [sumobot.scad]
2014-06-02 Tab spacing fixes
    [sumobot.scad]
2014-06-02 Basic bottom and top
    [sumobot.scad]
2014-06-02 Removing dupe function
    [sumobot.scad]
2014-06-02 Adding SoccerBot mod
    [WheelHub.scad, WheelHub.stl]
2014-06-03 Added arduino holes
    [sumobot.scad]
2014-06-03 Fine tuning for fit,
    [sumobot.scad]
2014-06-03 Added ziptie and caster holes
    [sumobot.scad]
2014-06-04 Adjusted arduino holes
    [sumobot.scad]
2014-06-04 Added shovel
    [sumobot.scad]
2014-06-04 Added a built in caster
    [sumobot.scad]
2014-06-04 Fixing up sled length
    [sumobot.scad]
2014-06-04 Pinoccio mount
    [sumobot.scad]
2014-06-04 Redesigned pinoccio mount
    [sumobot.scad]
2014-06-04 Resizing a bit
    [sumobot.scad]
2014-06-04 Added shovel sides. Moved bottom tabs.
    [sumobot.scad]
2014-06-04 Fixing up length
    [sumobot.scad]
2014-06-04 Pinoccio Top
    [sumobot.scad]
2014-06-05 Resized bottom tabs
    [sumobot.scad]
2014-06-05 Pinoccio height. Tweaks.,
    [sumobot.scad]
2014-06-05 Was using wrong width
    [sumobot.scad]
2014-06-05 Caster size
    [sumobot.scad]
2014-06-05 Added a wheel
    [sumobot.scad]
2014-06-05 Fixed width on top
    [sumobot.scad]
2014-06-19 added ponoko 5mm cutting plans with soccer mods
2014-06-25 Added 3D print files
    [bottom.stl, front-curved.stl, front-flat.stl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]
2014-06-26 updated cut lines for soccer but shovel
2014-07-01 Added a laser_sheet module to generate DXF files for laser cutting.
    [sumobot.scad]
2014-07-08 Added wheel hub for square wheel holes
    [WheelHub.stl]
2014-07-10 Fixed laser sheet layout. Shovel width.
    [sumobot.scad]
2014-07-11 Fixed shovel dimensions.
    [front-curved.stl, front-flat.stl, sumobot.scad]
2014-07-27 add stop cmd to example queue to avoid confusion when trying to understand
    [sumobot-sync.js]
2014-07-28 missing robot prefix in stop method
    [sumobot-sync.js]
2014-07-28 case switch easier to read
2014-07-28 Added SpringRC servo note
2014-07-29 break was in wrong spot in choreography example
    [sumobot-sync.js]
2015-05-10 Adding super-annotated openSCAD file
    [sumobot.scad]
2015-06-04 Adding 0.05 kerf as default
    [sumobot.scad]
2016-05-20 Update README.md
    Added link to DC motor adaptors
